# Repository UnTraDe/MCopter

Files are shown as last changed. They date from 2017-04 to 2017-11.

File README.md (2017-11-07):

# MCopter

A quadcopter built from scratch.

Currently there is a working PCB for the flight controller + basic firmware.

### Working (kind-of) features--

* Simple PID flight stabilization
* Radio communication via external radio module (both controlling the copter and sending telemtry data to the controller
* Simple remote controller made out of an old RC toy radio + arduino pro mini + nRF24

### Planned

* Designing custom frame and 3D print it
* Using an embedded radio solution (probably nRF24 based)
* Using 9-axis fusion instead of 6-axis to avoid yaw drift.

# The Hardware



This is version 2.0 of the flight controller PCB.
The PCB is design with 2 layers to keep down the cost, in the future I might redesign it with 4 layers to make it smaller. I'm also using 0805 to allow for easy hand-soldering.

The microcontroller is STM32F410RBT, a powerful 32-bit ARM Cortex M4 with hardware floating point unit and a lot of useful peripherals.

Other major components (sensors):

* ICM-20689; MEMES gyroscope + accelerometer. This is the newer generation of the popular MPU-6050 used in a lot of commercial flight controllers.
* MAG3110; A magnetometer.
* MS5637; A Barometer

The ICM-20689 togheter with the MAG3110 can be used for 9-axis fusion to provide better heading, avoid yaw drifting and togheter with the barometer also have an height based control instead of throttle based one.



* TODO take a better picture...

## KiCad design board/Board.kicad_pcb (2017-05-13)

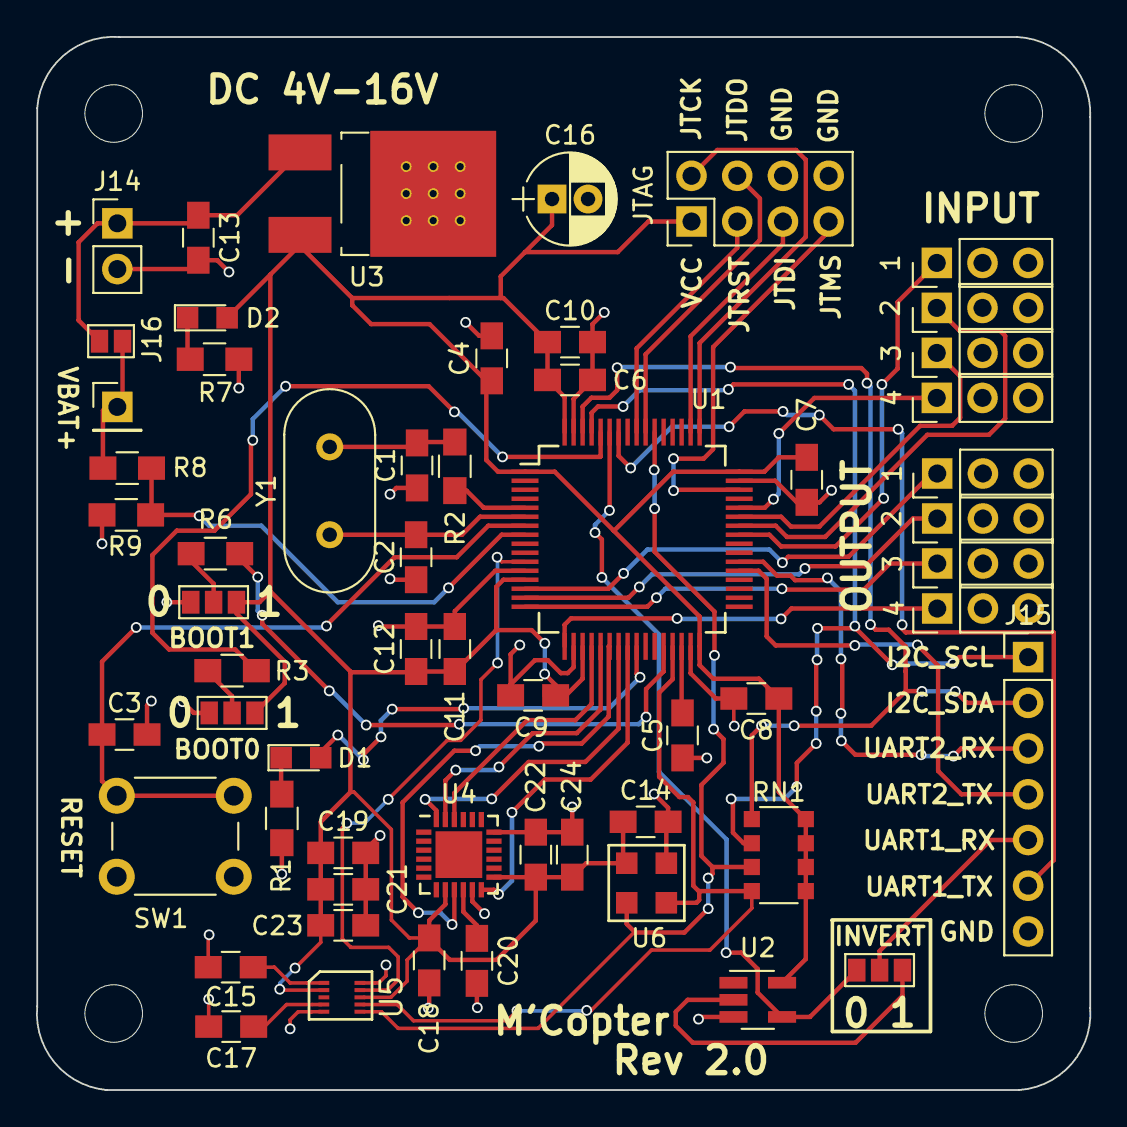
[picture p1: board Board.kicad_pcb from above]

Board: 2 copper layers, 58.5 x 58.5 mm, 54 parts (0 on the bottom side), 45 nets.

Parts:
1, 1#2, 2, 2#2, 3, 3#2, 4, 4#2: CONN_01X03; Pin_Header_Straight_1x03_Pitch2.54mm
C1, C2: 20pF; C_0805_HandSoldering
C3, C4, C6, C7, C8, C9, C12, C14, C15, C17, C21, C23, C24: 100nF; C_0805_HandSoldering
C5, C10: 4.7uF; C_0805_HandSoldering
C11, C19: 1uF; C_0805_HandSoldering
C13: 0.1uF; C_0805_HandSoldering
C16: 2.2uF; CP_Radial_D5.0mm_P2.00mm
C18: 10nF; C_0805_HandSoldering
C20: 0.47uF; C_0805_HandSoldering
C22: 2.2uF; C_0805_HandSoldering
D1, D2: LED; LED_0805
J14: CONN_01X02; Pin_Header_Straight_1x02_Pitch2.54mm
J15: CONN_01X07; Pin_Header_Straight_1x07_Pitch2.54mm
J16: GS2
JTAG: CONN_02X04; Pin_Header_Straight_2x04_Pitch2.54mm
R1: 22; R_0805_HandSoldering
R2: 0; R_0805_HandSoldering
R3, R6: 10K; R_0805_HandSoldering
R7: 220; R_0805_HandSoldering
R8: 62K; R_0805_HandSoldering
R9: 22K; R_0805_HandSoldering
RN1: 4.7K; R_Array_Convex_4x1206
SW1: SW_Push; SW_PUSH_6mm
U1: STM32F410RBTx; LQFP-64_10x10mm_Pitch0.5mm_handsoldering
U2: SN74LVC1G04; SOT-23-5_HandSoldering
U3: LF33ABDT-TR; TO-252-2Lead
U4: ICM-20689; QFN-24-1EP_4x4mm_Pitch0.5mm
U5: MAG3110; DFN_2x2mm_10pin_0.4pitch
U6: MS5637
Y1: 25 MHz; Crystal_HC49-U_Vertical

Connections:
+BATT: C13.1, J14.1, J16.1, U3.1
BATT_ADC: R8.2, R9.1, U1.8
GND: 1.3, 1#2.3, 2.3, 2#2.3, 3.3, 3#2.3, 4.3, 4#2.3, C1.1, C2.1, C3.2, C4.2, C5.2, C6.2, C7.2, C8.2, C9.2, C10.2, C11.2, C12.2, C13.2, C14.2, C15.2, C16.2, C17.2, C18.2, C19.2, C20.2, C21.2, C22.2, C23.2, C24.2, J14.2, J15.7, JTAG.6, JTAG.8, R1.2, R7.2, R9.2, SW1.1, U1.12, U1.18, U1.31, U1.47, U1.63, U2.3, U3.2, U4.11, U4.18, U5.5, U5.10, U6.4
I2C1_SCL: J15.1, RN1.2, U1.61
I2C1_SDA: J15.2, RN1.1, U1.62
I2C2_SCL: RN1.4, U1.29, U5.7, U6.3
I2C2_SDA: RN1.3, U1.54, U5.6, U6.2
ICM_INT: U1.24, U4.12
ICM_SPI_CS: U1.20, U4.22
ICM_SPI_MISO: U1.22, U4.9
ICM_SPI_MOSI: U1.23, U4.24
ICM_SPI_SCK: U1.21, U4.23
JTCK: JTAG.2, U1.49
JTDI: JTAG.5, U1.50
JTDO: JTAG.4, U1.55
JTMS: JTAG.7, U1.46
JTRST: JTAG.3, U1.56
MAG_INT: U1.11, U5.9
unnamed: C1.2, R2.1, Y1.2
unnamed: C2.2, U1.6, Y1.1
unnamed: C3.1, SW1.2, U1.7
unnamed: C5.1, U1.30
unnamed: C15.1, U5.1
unnamed: C17.1, U5.4
unnamed: C20.1, U4.10
unnamed: D1.1, R1.1
unnamed: D1.2, U1.25
unnamed: D2.1, R7.1
unnamed: J16.2, R8.1
unnamed: R2.2, U1.5
unnamed: R3.2, U1.60
unnamed: R6.1, U1.28
PWM_INPUT_1: 1#2.1, U1.41
PWM_INPUT_2: 2#2.1, U1.42
PWM_INPUT_3: 3#2.1, U1.43
PWM_INPUT_4: 4#2.1, U1.44
PWM_OUTPUT_1: 1.1, U1.14
PWM_OUTPUT_2: 2.1, U1.15
PWM_OUTPUT_3: 3.1, U1.16
PWM_OUTPUT_4: 4.1, U1.17
UART1_RX: U1.59, U2.4
UART1_TX: J15.6, U1.58
UART2_RX: J15.3, U1.38
UART2_TX: J15.4, U1.37
VCC: C4.1, C6.1, C7.1, C8.1, C9.1, C10.1, C11.1, C12.1, C14.1, C16.1, C18.1, C19.1, C21.1, C22.1, C23.1, C24.1, D2.2, JTAG.1, RN1.5, RN1.6, RN1.7, RN1.8, U1.1, U1.13, U1.19, U1.32, U1.48, U1.64, U2.5, U3.3, U4.8, U4.13, U5.2, U5.8, U6.1

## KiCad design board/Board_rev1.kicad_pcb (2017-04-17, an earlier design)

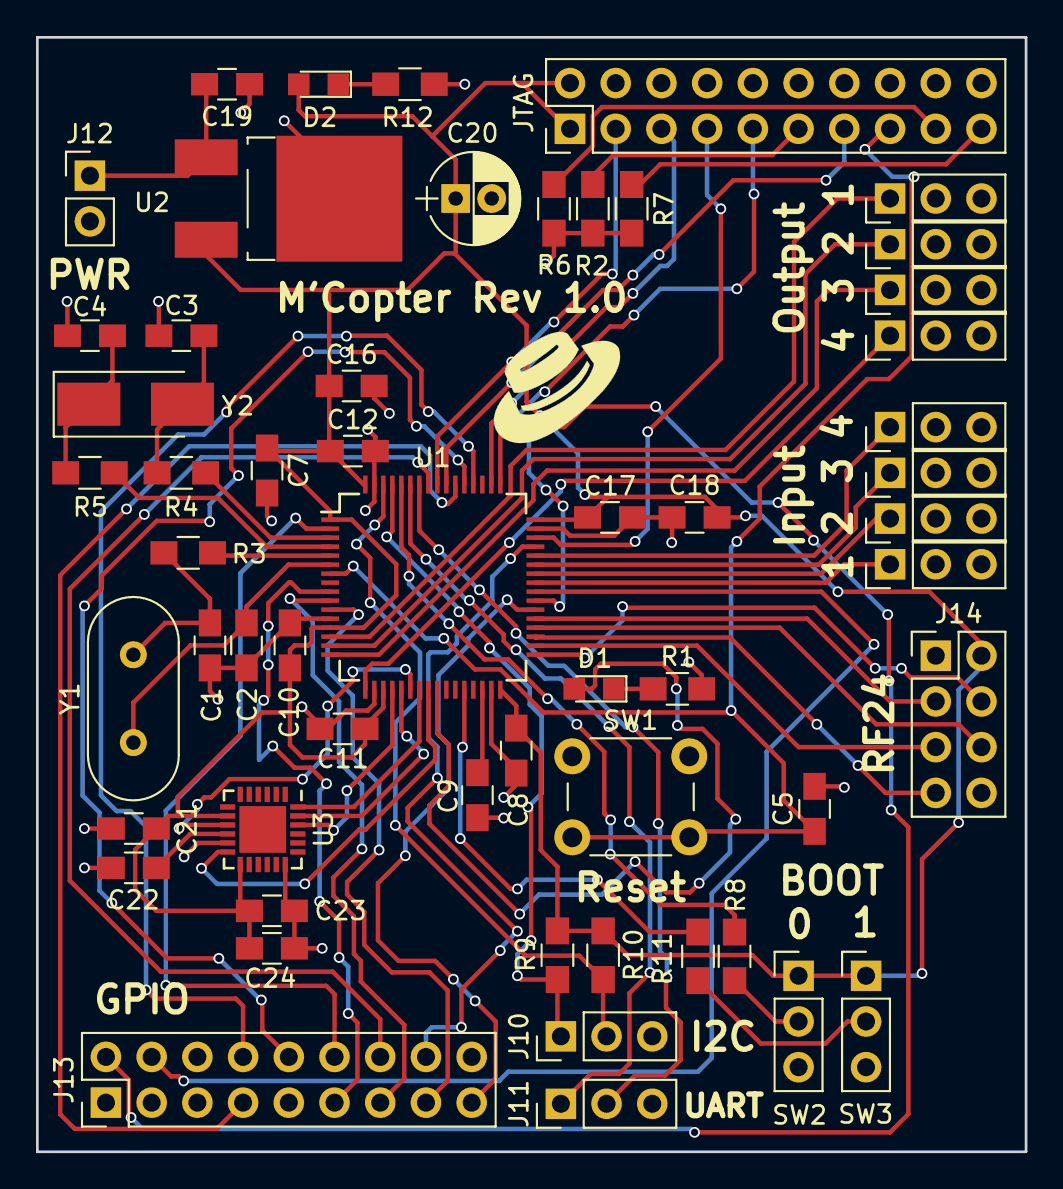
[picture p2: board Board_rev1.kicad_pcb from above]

Board: 2 copper layers, 54.9 x 61.9 mm, 48 parts (0 on the bottom side), 54 nets.

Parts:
C1, C2: 20pF; C_0805_HandSoldering
C3, C4: 1.5pF; C_0805_HandSoldering
C5, C7, C8, C10, C11, C12, C18, C24: 100nF; C_0805_HandSoldering
C9, C16: 4.7uF; C_0805_HandSoldering
C17: 1uF; C_0805_HandSoldering
C19: 0.1uF; C_0805_HandSoldering
C20: 2.2uF; CP_Radial_D5.0mm_P2.00mm
C21: 10nF; C_0805_HandSoldering
C22: 0.47uF; C_0805_HandSoldering
C23: 2.2uF; C_0805_HandSoldering
D1, D2: LED; LED_0805
J10, J11: CONN_01X03; Pin_Header_Straight_1x03_Pitch2.54mm
J12: CONN_01X02; Pin_Header_Straight_1x02_Pitch2.54mm
J13: CONN_02X09; Pin_Header_Straight_2x09_Pitch2.54mm
J14: CONN_02X04; Pin_Header_Straight_2x04_Pitch2.54mm
JTAG: CONN_02X10; Pin_Header_Straight_2x10_Pitch2.54mm
R1: 22; R_0805_HandSoldering
R2, R6, R7, R8, R9, R10, R11: 10K; R_0805_HandSoldering
R3, R4, R5: 0; R_0805_HandSoldering
R12: 220; R_0805_HandSoldering
SW1: SW_Push; SW_PUSH_6mm
SW2, SW3: SW_SPDT; Pin_Header_Straight_1x03_Pitch2.54mm
U1: STM32F410RBTx; LQFP-64_10x10mm_Pitch0.5mm
U2: LF33ABDT-TR; TO-252-2Lead
U3: ICM-20689; QFN-24-1EP_4x4mm_Pitch0.5mm
Y1: 25 MHz; Crystal_HC49-U_Vertical
Y2: 32.768 KHz; Crystal_SMD_5032-2pin_5.0x3.2mm_HandSoldering

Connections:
+12V: C19.1, J12.1, U2.1
GND: C1.1, C2.1, C3.1, C4.1, C5.2, C7.2, C8.2, C9.2, C10.2, C11.2, C12.2, C16.2, C17.2, C18.2, C19.2, C20.2, C21.2, C22.2, C23.2, C24.2, J10.3, J11.3, J12.2, J13.18, J14.1, JTAG.4, JTAG.6, JTAG.8, JTAG.10, JTAG.12, JTAG.14, JTAG.16, JTAG.18, JTAG.20, R1.2, R2.2, R6.2, R7.2, R12.2, SW1.1, SW2.3, SW3.3, U1.12, U1.18, U1.31, U1.47, U1.63, U2.2, U3.11, U3.18
I2C_SCL: J10.1, R9.2, U1.61
I2C_SDA: J10.2, R10.2, U1.62
ICM_INT: U1.24, U3.12
ICM_SPI_CS: U1.20, U3.22
ICM_SPI_MISO: U1.22, U3.9
ICM_SPI_MOSI: U1.23, U3.24
ICM_SPI_SCK: U1.21, U3.23
JTCK: JTAG.9, U1.49
JTDI: JTAG.5, U1.50
JTDO: JTAG.13, U1.55
JTMS: JTAG.7, U1.46
JTRST: JTAG.3, U1.56
NRF24_CE: J14.3, U1.37
NRF24_SPI_CS: J14.4, U1.33
NRF24_SPI_MISO: J14.7, U1.35
NRF24_SPI_MOSI: J14.6, U1.36
NRF24_SPI_SCK: J14.5, U1.34
NRST: C5.1, JTAG.15, SW1.2, U1.7
unnamed: C1.2, R3.1, Y1.2
unnamed: C2.2, U1.6, Y1.1
unnamed: C3.2, R4.1, Y2.2
unnamed: C4.2, R5.1, Y2.1
unnamed: C9.1, U1.30
unnamed: C22.1, U3.10
unnamed: D1.1, R1.1
unnamed: D1.2, U1.25
unnamed: D2.1, R12.1
unnamed: JTAG.11, R2.1
unnamed: JTAG.17, R6.1
unnamed: JTAG.19, R7.1
unnamed: R3.2, U1.5
unnamed: R4.2, U1.3
unnamed: R5.2, U1.4
unnamed: R8.1, SW2.2
unnamed: R8.2, U1.60
unnamed: R11.1, U1.28
unnamed: R11.2, SW3.2
PA12: J13.16, U1.45
PB5: J13.14, U1.57
PB11: J13.7, U1.54
PC1: J13.11, U1.9
PC2: J13.13, U1.10
PC3: J13.15, U1.11
PC7: J13.17, U1.38
PC8: J13.2, U1.39
PC9: J13.4, U1.40
PC11: J13.8, U1.52
PC12: J13.10, U1.53
PC13: J13.12, U1.2
UART_RX: J11.1, U1.59
UART_TX: J11.2, U1.58
VCC: C7.1, C8.1, C10.1, C11.1, C12.1, C16.1, C17.1, C18.1, C20.1, C21.1, C23.1, C24.1, D2.2, J14.2, JTAG.1, JTAG.2, R9.1, R10.1, SW2.1, SW3.1, U1.1, U1.13, U1.19, U1.32, U1.48, U1.64, U2.3, U3.8, U3.13

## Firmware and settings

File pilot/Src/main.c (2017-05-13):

/**
  ******************************************************************************
  * File Name          : main.c
  * Description        : Main program body
  ******************************************************************************
  *
  * COPYRIGHT(c) 2017 STMicroelectronics
  *
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
  ******************************************************************************
  */
/* Includes ------------------------------------------------------------------*/
#include "main.h"
#include "stm32f4xx_hal.h"

/* USER CODE BEGIN Includes */

#include <string.h>

#include "ICM20689.h"
#include "MS5637.h"
#include "AxisFusion.h"
#include "Common.h"
#include "Quaternion.h"
#include "Motors.h"
#include "PID.h"

/* USER CODE END Includes */

ADC_HandleTypeDef hadc1;

I2C_HandleTypeDef hi2c1;
I2C_HandleTypeDef hi2c2;

SPI_HandleTypeDef hspi1;
SPI_HandleTypeDef hspi2;

TIM_HandleTypeDef htim1;
TIM_HandleTypeDef htim5;

UART_HandleTypeDef huart1;
UART_HandleTypeDef huart6;
DMA_HandleTypeDef hdma_usart1_rx;

void SystemClock_Config(void);
void Error_Handler(void);
static void MX_GPIO_Init(void);
static void MX_DMA_Init(void);
static void MX_I2C1_Init(void);
static void MX_SPI1_Init(void);
static void MX_SPI2_Init(void);
static void MX_TIM1_Init(void);
static void MX_TIM5_Init(void);
static void MX_USART1_UART_Init(void);
static void MX_USART6_UART_Init(void);
static void MX_I2C2_Init(void);
static void MX_ADC1_Init(void);

void HAL_TIM_MspPostInit(TIM_HandleTypeDef *htim);
                                

/* USER CODE BEGIN 0 */

static const float Kp = 3.0f;
static const float Ki = 0.08f;
static const float Kd = 10.0f;
static const float i_limit = 100.0f;

static const float Kp_yaw = 8.0f;
static const float Ki_yaw = 0.4f;
static const float Kd_yaw = 0.0f;
static const float i_limit_yaw = 40.0f;

static const float _control_angle = 30.0f;
static const float _yaw_max_rate = 60.0f;

static volatile uint8_t _imu_data_ready = 0;
static volatile uint16_t _missed_imu_data = 0;

static float _orientation[4] = { 1.0f, 0.0f, 0.0f, 0.0f }; // Quaternion
static float _reference_orientation[4] = { 1.0f, 0.0f, 0.0f, 0.0f };

static uint16_t _throttle = 0;
static float _target_yaw_rate = 0.0f;
static float _target_pitch = 0.0f;
static float _target_roll = 0.0f;

static PID _pid_pitch;
static PID _pid_roll;
static PID _pid_yaw;

static volatile uint8_t _receiver_data_ready = 0;
static volatile struct
{
	uint16_t channels[16];
	uint8_t fail_safe;
} _receiver_data;

#define BATTERY_VOLTAGE_PERIOD		1000
#define BATTERY_LOW_THRESHOLD		10.8f
#define BATTERY_VOLTAGE_MULTIPLIER	3.794f
#define THROTTLE_THRESHOLD			150

#define SBUS_CHANNEL_MIN 				172
#define SBUS_CHANNEL_MAX 				1811
#define SBUS_CHANENL_RANGE				(SBUS_CHANNEL_MAX - SBUS_CHANNEL_MIN)

void HAL_GPIO_EXTI_Callback(uint16_t GPIO_Pin)
{
	if (GPIO_Pin == GPIO_PIN_4)
	{
		// TODO need to disable interrupts before doing SPI stuff?
		
		if (!_imu_data_ready)
		{
			if (ICM20689_DataReady())
				_imu_data_ready = 1;
		}
		else
		{
			_missed_imu_data++;
		}
		
		// TODO handle cases where the interrupt was generated because of another reason... 
	}	
}

static uint8_t _uart_rx_data_buffer[32];
static uint8_t _uart_tx_data_buffer[32];

void HAL_UART_RxCpltCallback(UART_HandleTypeDef* huart)
{
	if (!_receiver_data_ready)
	{
		if (_uart_rx_data_buffer[0] == 0x0F && _uart_rx_data_buffer[24] == 0x00)
		{
			uint8_t* payload = &_uart_rx_data_buffer[1];
		
			_receiver_data.channels[0]  = (uint16_t)((payload[0]    | payload[1] << 8) & 0x07FF);
			_receiver_data.channels[1]  = (uint16_t)((payload[1] >> 3 | payload[2] << 5) & 0x07FF);
			_receiver_data.channels[2]  = (uint16_t)((payload[2] >> 6 | payload[3] << 2 | payload[4] << 10) & 0x07FF);
			_receiver_data.channels[3]  = (uint16_t)((payload[4] >> 1 | payload[5] << 7) & 0x07FF);
			_receiver_data.channels[4]  = (uint16_t)((payload[5] >> 4 | payload[6] << 4) & 0x07FF);
			_receiver_data.channels[5]  = (uint16_t)((payload[6] >> 7 | payload[7] << 1 | payload[8] << 9) & 0x07FF);
			_receiver_data.channels[6]  = (uint16_t)((payload[8] >> 2 | payload[9] << 6) & 0x07FF);
			_receiver_data.channels[7]  = (uint16_t)((payload[9] >> 5 | payload[10] << 3) & 0x07FF);
			_receiver_data.channels[8]  = (uint16_t)((payload[11]   | payload[12] << 8) & 0x07FF);
			_receiver_data.channels[9]  = (uint16_t)((payload[12] >> 3 | payload[13] << 5) & 0x07FF);
			_receiver_data.channels[10] = (uint16_t)((payload[13] >> 6 | payload[14] << 2 | payload[15] << 10) & 0x07FF);
			_receiver_data.channels[11] = (uint16_t)((payload[15] >> 1 | payload[16] << 7) & 0x07FF);
			_receiver_data.channels[12] = (uint16_t)((payload[16] >> 4 | payload[17] << 4) & 0x07FF);
			_receiver_data.channels[13] = (uint16_t)((payload[17] >> 7 | payload[18] << 1 | payload[19] << 9) & 0x07FF);
			_receiver_data.channels[14] = (uint16_t)((payload[19] >> 2 | payload[20] << 6) & 0x07FF);
			_receiver_data.channels[15] = (uint16_t)((payload[20] >> 5 | payload[21] << 3) & 0x07FF);
			
			_receiver_data.fail_safe = (payload[22] & 0x08);
		
			_receiver_data_ready = 1;
		}
	}
	else
	{
		// TODO increment some dropped counter
	}
	
	// TODO can this be replaced by configuring the DMA as circular?
	HAL_UART_Receive_DMA(&huart1, _uart_rx_data_buffer, 25);
}

static void CalculateBias(float* gyro_bias, float* accel_bias);

/* USER CODE END 0 */

int main(void)
{

  /* MCU Configuration----------------------------------------------------------*/

  /* Reset of all peripherals, Initializes the Flash interface and the Systick. */
	HAL_Init();

	  /* Configure the system clock */
	SystemClock_Config();

	  /* Initialize all configured peripherals */
	MX_GPIO_Init();
	MX_DMA_Init();
	MX_I2C1_Init();
	MX_SPI1_Init();
	MX_SPI2_Init();
	MX_TIM1_Init();
	MX_TIM5_Init();
	MX_USART1_UART_Init();
	MX_USART6_UART_Init();
	MX_I2C2_Init();
	MX_ADC1_Init();

	  /* USER CODE BEGIN 2 */
	Motors_Init(&htim5);
	
	uint8_t error = ICM20689_Init(&hspi1, GPIOA, GPIO_PIN_4);
	
	if (error)
	{
		while (1)
		{
			HAL_GPIO_TogglePin(GPIOC, GPIO_PIN_5);
			HAL_Delay(500);
		}
	}
	
	_pid_pitch.kp = Kp;
	_pid_pitch.ki = Ki;
	_pid_pitch.kd = Kd;
	_pid_pitch.i_limit = i_limit;
	_pid_pitch.error_sum = 0.0f;
	_pid_pitch.last_error = 0.0f;
	_pid_pitch.error = 0.0f;
	_pid_pitch.error_rate = 0.0f;
	
	_pid_roll.kp = Kp;
	_pid_roll.ki = Ki;
	_pid_roll.kd = Kd;
	_pid_roll.i_limit = i_limit;
	_pid_roll.error_sum = 0.0f;
	_pid_roll.last_error = 0.0f;
	_pid_roll.error = 0.0f;
	_pid_roll.error_rate = 0.0f;
	
	_pid_yaw.kp = Kp_yaw;
	_pid_yaw.ki = Ki_yaw;
	_pid_yaw.kd = Kd_yaw;
	_pid_yaw.i_limit = i_limit_yaw;
	_pid_yaw.error_sum = 0.0f;
	_pid_yaw.last_error = 0.0f;
	_pid_yaw.error = 0.0f;
	_pid_yaw.error_rate = 0.0f;
	
  /* USER CODE END 2 */

  /* Infinite loop */
  /* USER CODE BEGIN 3 */
	
	

	float gyro_bias[3] = { 0.503540, 1.441956, 0.129700 };
	float accel_bias[3] = { -0.000305, -0.004944, 0.017456 };
//	CalculateBias(gyro_bias, accel_bias);
//	
//	uint8_t output[128] = { 0 };
//	sprintf((char*)output, "%f, %f, %f\r\n%f, %f, %f\r\n", gyro_bias[0], gyro_bias[1], gyro_bias[2], accel_bias[0], accel_bias[1], accel_bias[2]);
//	HAL_UART_Transmit(&huart6, output, strlen((char*)output), 100);
	
	gyro_bias[0] *= -1;
	gyro_bias[1] *= -1;
	gyro_bias[2] *= -1;
	ICM20689_SetLocalGyroBias(gyro_bias);
	
	accel_bias[0] *= -1;
	accel_bias[1] *= -1;
	accel_bias[2] *= -1;
	ICM20689_SetLocalAccelBias(accel_bias);
	
	// SBUS is sending every 4 ms, so we wait to synchronize
	
	while (1)
	{
		if (HAL_TIMEOUT == HAL_UART_Receive(&huart1, _uart_rx_data_buffer, 1, 2))
		{
			HAL_UART_Receive_DMA(&huart1, _uart_rx_data_buffer, 25);
			break;
		}
	}
	
	uint8_t fail_safe = 1;
	
	uint32_t now = HAL_GetTick();
	uint32_t last = now;
	
	uint32_t battery_voltage_timer = 0;
	uint32_t test_timer = 0;
	uint32_t hz_timer = 0;
	
	uint32_t hz_counter = 0;
	
	uint8_t cmd;
	
	// Barometer test
	
	//MS5637_Init(&hi2c2, 0x76);
	
//	cmd = 0x1E;
//	if (HAL_I2C_Master_Transmit(&hi2c2, 0b11101100, &cmd, 1, 100) != HAL_OK)
//	{
//		while (1)
//		{
//			HAL_GPIO_TogglePin(GPIOC, GPIO_PIN_5);
//			HAL_Delay(500);
//		}
//	}
//	
//	cmd = 0xA0;
//	HAL_I2C_Master_Transmit(&hi2c2, 0b11101100, &cmd, 1, 100);
//	uint16_t data = 0;
//	HAL_I2C_Master_Receive(&hi2c2, 0b11101101, (uint8_t*)&data, 2, 100);
	
	// Magnetometer test
	
//	cmd = 0x07;
//	HAL_I2C_Master_Transmit(&hi2c2, 0x0E << 1, &cmd, 1, 100);
//	uint8_t id = 0;
//	HAL_I2C_Master_Receive(&hi2c2, (0x0E << 1) | 0x01, (uint8_t*)&id, 1, 100);
	
	float battery_voltage = 12.6f;
	float battery_voltage_idle = 12.6f;
	
	// TODO intialize those with actual values from the ADC
	
	while (1)
	{
		now = HAL_GetTick(); // TODO handle rollover
		uint32_t dt_ms = now - last;
		last = now;
		
		battery_voltage_timer += dt_ms;
		test_timer += dt_ms;
		hz_timer += dt_ms;
		
		if (_receiver_data_ready)
		{
			uint16_t throttle = ((_receiver_data.channels[0] - SBUS_CHANNEL_MIN) / (float)SBUS_CHANENL_RANGE) * 1000.0f;
			
			if (throttle > 800)
				_throttle = 800;
			else
				_throttle = throttle;
			
//			
//			if (throttle > 500)
//				throttle = 1000;
//			else
//				throttle = 0;
//			
//			float motors[4];
//			
//			motors[0] = throttle; // Back Right
//			motors[1] = throttle; // Back Left
//			motors[2] = throttle; // Front Right
//			motors[3] = throttle; // Front Left
//
//			Motors_Set(motors);
			
			_target_yaw_rate = ((_receiver_data.channels[3] - SBUS_CHANNEL_MIN) * (_yaw_max_rate / SBUS_CHANENL_RANGE)) - (_yaw_max_rate / 2.0f);
			_target_pitch = ((_receiver_data.channels[2] - SBUS_CHANNEL_MIN) * (_control_angle / SBUS_CHANENL_RANGE)) - (_control_angle / 2.0f);
			_target_roll = ((_receiver_data.channels[1] - SBUS_CHANNEL_MIN) * (_control_angle / SBUS_CHANENL_RANGE)) - (_control_angle / 2.0f);

			_target_yaw_rate *= -1;
			
			fail_safe = _receiver_data.fail_safe;
			
//			if (test_timer >= 10)
//			{
//				test_timer = 0;
//				uint8_t output[32] = { 0 };
//				sprintf((char*)output, "%f, %f, %f\r\n", _target_pitch, _target_yaw_rate, _target_roll);
//				HAL_UART_Transmit(&huart6, output, strlen((char*)output), 100);
//			}
			
			_receiver_data_ready = 0;
		}
		
//		if (test_timer >= 10)
//		{
//			test_timer = 0;
//			uint8_t output[64] = { 0 };
//			sprintf((char*)output, "%d, %d\r\n", fail_safe, _throttle);
//			HAL_UART_Transmit(&huart6, output, strlen((char*)output), 1000);
//		}
		
		if (fail_safe)
		{
			float motors[4] = { 0 };
			Motors_Set(motors);
			continue;
		}
		
//		if (battery_voltage_timer >= BATTERY_VOLTAGE_PERIOD)
//		{
//			battery_voltage_timer = 0;
//			
//			HAL_StatusTypeDef status = HAL_ADC_Start(&hadc1);
//			status = HAL_ADC_PollForConversion(&hadc1, 10);
//		
//			if (status != HAL_TIMEOUT)
//			{
//				uint32_t val = HAL_ADC_GetValue(&hadc1);
//				float voltage = (3.3f / 4096.0f) * val;
//				battery_voltage = voltage * BATTERY_VOLTAGE_MULTIPLIER;
//				
//				if (_throttle < THROTTLE_THRESHOLD)
//					battery_voltage_idle = voltage * BATTERY_VOLTAGE_MULTIPLIER;
//				
////				uint8_t output[64] = { 0 };
////				sprintf((char*)output, "%d, %f, %f\r\n", _throttle, battery_voltage, battery_voltage_idle);
////				HAL_UART_Transmit(&huart6, output, strlen((char*)output), 1000);
//				
//				// TODO averaging samples?
//			}
//			else
//			{
//				battery_voltage = 0.0f;
//			}
//		
//			HAL_ADC_Stop(&hadc1);
//		}
		
//		if (battery_voltage_idle <= BATTERY_LOW_THRESHOLD)
//		{
//			float motors[4] = { 0 };
//			Motors_Set(motors);
//			
//			HAL_GPIO_WritePin(GPIOC, GPIO_PIN_5, GPIO_PIN_SET);
//			HAL_Delay(200);
//			HAL_GPIO_WritePin(GPIOC, GPIO_PIN_5, GPIO_PIN_RESET);
//			HAL_Delay(200);
//			HAL_GPIO_WritePin(GPIOC, GPIO_PIN_5, GPIO_PIN_SET);
//			HAL_Delay(200);
//			HAL_GPIO_WritePin(GPIOC, GPIO_PIN_5, GPIO_PIN_RESET);
//			HAL_Delay(1000);
//		}
		
		if (_imu_data_ready)
		{
			_imu_data_ready = 0;
			
			float gyro[3];
			float accel[3];
			ICM20689_ReadGyro(gyro);
			ICM20689_ReadAccel(accel);
//			
//			hz_counter++;
//			
//			if (hz_timer >= 1000)
//			{
//				hz_timer = 0;
//				uint8_t output[16] = { 0 };
//				sprintf((char*)output, "%d\r\n", hz_counter);
//				hz_counter = 0;
//				HAL_UART_Transmit(&huart6, output, strlen((char*)output), 100);
//			}
			
			AxisFusion_MahonyAHRSupdateIMU(_orientation, gyro[0]*PI / 180.0f, gyro[1]*PI / 180.0f, gyro[2]*PI / 180.0f, accel[0], accel[1], accel[2]);
		
			float quat[4];
			Quaternion_Multiply(_reference_orientation, _orientation, quat);
		
			float pitch, roll, yaw;
			Quaternion_ToEuler(quat, &pitch, &roll, &yaw);
		
			pitch *= 180.0f / PI;
			yaw *= 180.0f / PI;
			roll *= 180.0f / PI;
			
//			if (test_timer >= 100)
//			{
//				test_timer = 0;
//				uint8_t output[32] = { 0 };
//				sprintf((char*)output, "%.2f, %.2f, %.2f\r\n", pitch, yaw, roll);
//				HAL_UART_Transmit(&huart6, output, strlen((char*)output), 100);
//			}
			
			float output_pitch = 0.0f;
			float output_roll = 0.0f;
			float output_yaw = 0.0f;
			
			float dt_ms = 0.01f; // TODO IMPORTANTTTTTTTTTTTTTTTTTTTTTTTTTTTTTTTTTTTTTTTTTTTTTTTTTTTTTTTTTTTTTTTTTTTTT

			if (_throttle >= THROTTLE_THRESHOLD)
			{
				output_pitch = PID_Compute(&_pid_pitch, _target_pitch, pitch, dt_ms);
				output_roll = PID_Compute(&_pid_roll, _target_roll, roll, dt_ms);
				output_yaw = PID_Compute(&_pid_yaw, _target_yaw_rate, gyro[2] * (PI / 180.0f), dt_ms);
			}
			else
			{
				_pid_pitch.error_sum = 0.0f;
				_pid_roll.error_sum = 0.0f;
				_pid_yaw.error_sum = 0.0f;
			}
	
			float motors[4];
			
			motors[0] = _throttle + output_pitch - output_roll + output_yaw; // Back Right
			motors[1] = _throttle + output_pitch + output_roll - output_yaw; // Back Left
			motors[2] = _throttle - output_pitch - output_roll - output_yaw; // Front Right
			motors[3] = _throttle - output_pitch + output_roll + output_yaw; // Front Left
			
			Motors_Set(motors);
			
//			if (test_timer >= 10)
//			{
//				test_timer = 0;
//				uint8_t output[64] = { 0 };
//				sprintf((char*)output, "%.2f, %.2f, %.2f\r\n", output_pitch, output_roll, output_yaw);
//				HAL_UART_Transmit(&huart6, output, strlen((char*)output), 1000);
//			}
			
//			if (test_timer >= 10)
//			{
//				test_timer = 0;
//				uint8_t output[64] = { 0 };
//				sprintf((char*)output, "%.2f, %.2f, %.2f, %.2f\n", motors[0], motors[1], motors[2], motors[3]);
//				HAL_UART_Transmit(&huart6, output, strlen((char*)output), 1000);
//			}

			
		}
	}
	
  /* USER CODE END 3 */

}

/** System Clock Configuration
*/
void SystemClock_Config(void)
{

	RCC_OscInitTypeDef RCC_OscInitStruct;
	RCC_ClkInitTypeDef RCC_ClkInitStruct;

	    /**Configure the main internal regulator output voltage 
	    */
	__HAL_RCC_PWR_CLK_ENABLE();

	__HAL_PWR_VOLTAGESCALING_CONFIG(PWR_REGULATOR_VOLTAGE_SCALE1);

	    /**Initializes the CPU, AHB and APB busses clocks 
	    */
	RCC_OscInitStruct.OscillatorType = RCC_OSCILLATORTYPE_HSE;
	RCC_OscInitStruct.HSEState = RCC_HSE_ON;
	RCC_OscInitStruct.PLL.PLLState = RCC_PLL_ON;
	RCC_OscInitStruct.PLL.PLLSource = RCC_PLLSOURCE_HSE;
	RCC_OscInitStruct.PLL.PLLM = 12;
	RCC_OscInitStruct.PLL.PLLN = 96;
	RCC_OscInitStruct.PLL.PLLP = RCC_PLLP_DIV2;
	RCC_OscInitStruct.PLL.PLLQ = 4;
	RCC_OscInitStruct.PLL.PLLR = 2;
	if (HAL_RCC_OscConfig(&RCC_OscInitStruct) != HAL_OK)
	{
		Error_Handler();
	}

	    /**Initializes the CPU, AHB and APB busses clocks 
	    */
	RCC_ClkInitStruct.ClockType = RCC_CLOCKTYPE_HCLK | RCC_CLOCKTYPE_SYSCLK
	                            | RCC_CLOCKTYPE_PCLK1 | RCC_CLOCKTYPE_PCLK2;
	RCC_ClkInitStruct.SYSCLKSource = RCC_SYSCLKSOURCE_PLLCLK;
	RCC_ClkInitStruct.AHBCLKDivider = RCC_SYSCLK_DIV1;
	RCC_ClkInitStruct.APB1CLKDivider = RCC_HCLK_DIV4;
	RCC_ClkInitStruct.APB2CLKDivider = RCC_HCLK_DIV1;

	if (HAL_RCC_ClockConfig(&RCC_ClkInitStruct, FLASH_LATENCY_3) != HAL_OK)
	{
		Error_Handler();
	}

	    /**Configure the Systick interrupt time 
	    */
	HAL_SYSTICK_Config(HAL_RCC_GetHCLKFreq() / 1000);

	    /**Configure the Systick 
	    */
	HAL_SYSTICK_CLKSourceConfig(SYSTICK_CLKSOURCE_HCLK);

	  /* SysTick_IRQn interrupt configuration */
	HAL_NVIC_SetPriority(SysTick_IRQn, 0, 0);
}

/* ADC1 init function */
static void MX_ADC1_Init(void)
{

	ADC_ChannelConfTypeDef sConfig;

	    /**Configure the global features of the ADC (Clock, Resolution, Data Alignment and number of conversion) 
	    */
	hadc1.Instance = ADC1;
	hadc1.Init.ClockPrescaler = ADC_CLOCK_SYNC_PCLK_DIV4;
	hadc1.Init.Resolution = ADC_RESOLUTION_12B;
	hadc1.Init.ScanConvMode = DISABLE;
	hadc1.Init.ContinuousConvMode = DISABLE;
	hadc1.Init.DiscontinuousConvMode = DISABLE;
	hadc1.Init.ExternalTrigConvEdge = ADC_EXTERNALTRIGCONVEDGE_NONE;
	hadc1.Init.ExternalTrigConv = ADC_SOFTWARE_START;
	hadc1.Init.DataAlign = ADC_DATAALIGN_RIGHT;
	hadc1.Init.NbrOfConversion = 1;
	hadc1.Init.DMAContinuousRequests = DISABLE;
	hadc1.Init.EOCSelection = ADC_EOC_SINGLE_CONV;
	if (HAL_ADC_Init(&hadc1) != HAL_OK)
	{
		Error_Handler();
	}

	    /**Configure for the selected ADC regular channel its corresponding rank in the sequencer and its sample time. 
	    */
	sConfig.Channel = ADC_CHANNEL_10;
	sConfig.Rank = 1;
	sConfig.SamplingTime = ADC_SAMPLETIME_3CYCLES;
	if (HAL_ADC_ConfigChannel(&hadc1, &sConfig) != HAL_OK)
	{
		Error_Handler();
	}

}

/* I2C1 init function */
static void MX_I2C1_Init(void)
{

	hi2c1.Instance = I2C1;
	hi2c1.Init.ClockSpeed = 100000;
	hi2c1.Init.DutyCycle = I2C_DUTYCYCLE_2;
	hi2c1.Init.OwnAddress1 = 0;
	hi2c1.Init.AddressingMode = I2C_ADDRESSINGMODE_7BIT;
	hi2c1.Init.DualAddressMode = I2C_DUALADDRESS_DISABLE;
	hi2c1.Init.OwnAddress2 = 0;
	hi2c1.Init.GeneralCallMode = I2C_GENERALCALL_DISABLE;
	hi2c1.Init.NoStretchMode = I2C_NOSTRETCH_DISABLE;
	if (HAL_I2C_Init(&hi2c1) != HAL_OK)
	{
		Error_Handler();
	}

}

/* I2C2 init function */
static void MX_I2C2_Init(void)
{

	hi2c2.Instance = I2C2;
	hi2c2.Init.ClockSpeed = 400000;
	hi2c2.Init.DutyCycle = I2C_DUTYCYCLE_2;
	hi2c2.Init.OwnAddress1 = 0;
	hi2c2.Init.AddressingMode = I2C_ADDRESSINGMODE_7BIT;
	hi2c2.Init.DualAddressMode = I2C_DUALADDRESS_DISABLE;
	hi2c2.Init.OwnAddress2 = 0;
	hi2c2.Init.GeneralCallMode = I2C_GENERALCALL_DISABLE;
	hi2c2.Init.NoStretchMode = I2C_NOSTRETCH_DISABLE;
	if (HAL_I2C_Init(&hi2c2) != HAL_OK)
	{
		Error_Handler();
	}

}

/* SPI1 init function */
static void MX_SPI1_Init(void)
{

	hspi1.Instance = SPI1;
	hspi1.Init.Mode = SPI_MODE_MASTER;
	hspi1.Init.Direction = SPI_DIRECTION_2LINES;
	hspi1.Init.DataSize = SPI_DATASIZE_8BIT;
	hspi1.Init.CLKPolarity = SPI_POLARITY_HIGH;
	hspi1.Init.CLKPhase = SPI_PHASE_2EDGE;
	hspi1.Init.NSS = SPI_NSS_SOFT;
	hspi1.Init.BaudRatePrescaler = SPI_BAUDRATEPRESCALER_16;
	hspi1.Init.FirstBit = SPI_FIRSTBIT_MSB;
	hspi1.Init.TIMode = SPI_TIMODE_DISABLE;
	hspi1.Init.CRCCalculation = SPI_CRCCALCULATION_DISABLE;
	hspi1.Init.CRCPolynomial = 15;
	if (HAL_SPI_Init(&hspi1) != HAL_OK)
	{
		Error_Handler();
	}

}

/* SPI2 init function */
static void MX_SPI2_Init(void)
{

	hspi2.Instance = SPI2;
	hspi2.Init.Mode = SPI_MODE_MASTER;
	hspi2.Init.Direction = SPI_DIRECTION_2LINES;
	hspi2.Init.DataSize = SPI_DATASIZE_8BIT;
	hspi2.Init.CLKPolarity = SPI_POLARITY_LOW;
	hspi2.Init.CLKPhase = SPI_PHASE_1EDGE;
	hspi2.Init.NSS = SPI_NSS_SOFT;
	hspi2.Init.BaudRatePrescaler = SPI_BAUDRATEPRESCALER_2;
	hspi2.Init.FirstBit = SPI_FIRSTBIT_MSB;
	hspi2.Init.TIMode = SPI_TIMODE_DISABLE;
	hspi2.Init.CRCCalculation = SPI_CRCCALCULATION_DISABLE;
	hspi2.Init.CRCPolynomial = 15;
	if (HAL_SPI_Init(&hspi2) != HAL_OK)
	{
		Error_Handler();
	}

}

/* TIM1 init function */
static void MX_TIM1_Init(void)
{

	TIM_MasterConfigTypeDef sMasterConfig;
	TIM_IC_InitTypeDef sConfigIC;

	htim1.Instance = TIM1;
	htim1.Init.Prescaler = 0;
	htim1.Init.CounterMode = TIM_COUNTERMODE_UP;
	htim1.Init.Period = 0;
	htim1.Init.ClockDivision = TIM_CLOCKDIVISION_DIV1;
	htim1.Init.RepetitionCounter = 0;
	if (HAL_TIM_IC_Init(&htim1) != HAL_OK)
	{
		Error_Handler();
	}

	sMasterConfig.MasterOutputTrigger = TIM_TRGO_RESET;
	sMasterConfig.MasterSlaveMode = TIM_MASTERSLAVEMODE_DISABLE;
	if (HAL_TIMEx_MasterConfigSynchronization(&htim1, &sMasterConfig) != HAL_OK)
	{
		Error_Handler();
	}

	sConfigIC.ICPolarity = TIM_INPUTCHANNELPOLARITY_RISING;
	sConfigIC.ICSelection = TIM_ICSELECTION_DIRECTTI;
	sConfigIC.ICPrescaler = TIM_ICPSC_DIV1;
	sConfigIC.ICFilter = 0;
	if (HAL_TIM_IC_ConfigChannel(&htim1, &sConfigIC, TIM_CHANNEL_1) != HAL_OK)
	{
		Error_Handler();
	}

	if (HAL_TIM_IC_ConfigChannel(&htim1, &sConfigIC, TIM_CHANNEL_2) != HAL_OK)
	{
		Error_Handler();
	}

	if (HAL_TIM_IC_ConfigChannel(&htim1, &sConfigIC, TIM_CHANNEL_3) != HAL_OK)
	{
		Error_Handler();
	}

	if (HAL_TIM_IC_ConfigChannel(&htim1, &sConfigIC, TIM_CHANNEL_4) != HAL_OK)
	{
		Error_Handler();
	}

}

/* TIM5 init function */
static void MX_TIM5_Init(void)
{

	TIM_MasterConfigTypeDef sMasterConfig;
	TIM_OC_InitTypeDef sConfigOC;

	htim5.Instance = TIM5;
	htim5.Init.Prescaler = 0;
	htim5.Init.CounterMode = TIM_COUNTERMODE_UP;
	htim5.Init.Period = 125000;
	htim5.Init.ClockDivision = TIM_CLOCKDIVISION_DIV1;
	if (HAL_TIM_PWM_Init(&htim5) != HAL_OK)
	{
		Error_Handler();
	}

	sMasterConfig.MasterOutputTrigger = TIM_TRGO_RESET;
	sMasterConfig.MasterSlaveMode = TIM_MASTERSLAVEMODE_DISABLE;
	if (HAL_TIMEx_MasterConfigSynchronization(&htim5, &sMasterConfig) != HAL_OK)
	{
		Error_Handler();
	}

	sConfigOC.OCMode = TIM_OCMODE_PWM1;
	sConfigOC.Pulse = 0;
	sConfigOC.OCPolarity = TIM_OCPOLARITY_HIGH;
	sConfigOC.OCFastMode = TIM_OCFAST_DISABLE;
	if (HAL_TIM_PWM_ConfigChannel(&htim5, &sConfigOC, TIM_CHANNEL_1) != HAL_OK)
	{
		Error_Handler();
	}

	if (HAL_TIM_PWM_ConfigChannel(&htim5, &sConfigOC, TIM_CHANNEL_2) != HAL_OK)
	{
		Error_Handler();
	}

	if (HAL_TIM_PWM_ConfigChannel(&htim5, &sConfigOC, TIM_CHANNEL_3) != HAL_OK)
	{
		Error_Handler();
	}

	if (HAL_TIM_PWM_ConfigChannel(&htim5, &sConfigOC, TIM_CHANNEL_4) != HAL_OK)
	{
		Error_Handler();
	}

	HAL_TIM_MspPostInit(&htim5);

}
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

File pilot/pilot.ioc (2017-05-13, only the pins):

Mcu.UserName=STM32F410RBTx
PA0-WKUP.Signal=S_TIM5_CH1
PA1.Signal=S_TIM5_CH2
PA10.Signal=S_TIM1_CH3
PA11.Signal=S_TIM1_CH4
PA13.Signal=SYS_JTMS-SWDIO
PA14.Signal=SYS_JTCK-SWCLK
PA15.Signal=SYS_JTDI
PA2.Signal=S_TIM5_CH3
PA3.Signal=S_TIM5_CH4
PA4.Signal=GPIO_Output
PA5.Signal=SPI1_SCK
PA6.Signal=SPI1_MISO
PA7.Signal=SPI1_MOSI
PA8.Signal=S_TIM1_CH1
PA9.Signal=S_TIM1_CH2
PB10.Signal=I2C2_SCL
PB11.Signal=I2C2_SDA
PB12.Signal=GPIO_Output
PB13.Signal=SPI2_SCK
PB14.Signal=SPI2_MISO
PB15.Signal=SPI2_MOSI
PB3.Signal=SYS_JTDO-SWO
PB4.Signal=SYS_JTRST
PB6.Signal=USART1_TX
PB7.Signal=USART1_RX
PB8.Signal=I2C1_SCL
PB9.Signal=I2C1_SDA
PC0.Signal=ADCx_IN10
PC4.Signal=GPXTI4
PC5.Signal=GPIO_Output
PC6.Signal=USART6_TX
PC7.Signal=USART6_RX

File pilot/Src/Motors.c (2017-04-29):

#include "Motors.h"

static TIM_HandleTypeDef* _htim;

#define PERIOD_MIN			50000
#define PERIOD_MAX			100000
#define PERIOD_RESOLUTION	(PERIOD_MAX - PERIOD_MIN)
#define MAX_VALUE			1000

// TODO currently using the PWM mode there's a delay from calling start to when the actual signal starts, depends on  ARR - CCRx

void Motors_Init(TIM_HandleTypeDef* htim)
{
	_htim = htim;
	
	_htim->Instance->CCR1 = PERIOD_MIN;
	_htim->Instance->CCR2 = PERIOD_MIN;
	_htim->Instance->CCR3 = PERIOD_MIN;
	_htim->Instance->CCR4 = PERIOD_MIN;
	
	HAL_TIM_PWM_Start(_htim, TIM_CHANNEL_1);
	HAL_TIM_PWM_Start(_htim, TIM_CHANNEL_2);
	HAL_TIM_PWM_Start(_htim, TIM_CHANNEL_3);
	HAL_TIM_PWM_Start(_htim, TIM_CHANNEL_4);
}

void Motors_Set(float* values)
{
	for (int i = 0; i < 4; i++)
	{
		float value = values[i];
		
		if (value > MAX_VALUE)
			value = MAX_VALUE;
		
		int output = PERIOD_MIN + ((PERIOD_RESOLUTION / MAX_VALUE) * value);
		
		switch (i)
		{
		case 0:
			_htim->Instance->CCR1 = output;
			break;
		case 1:
			_htim->Instance->CCR2 = output;
			break;
		case 2:
			_htim->Instance->CCR3 = output;
			break;
		case 3:
			_htim->Instance->CCR4 = output;
			break;
		}
	}
}

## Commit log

2017-04-17 configure timers
2017-04-17 completed motors
2017-04-17 connected PID loop
2017-04-17 reading SBUS with DMA
2017-04-18 uart signal inverter; battery measurement
    [Board.sch]
2017-04-18 inverter gate is now optional
    [Board.sch]
2017-04-18 pcb rev2, work in progress
    [Board.kicad_pcb, Board.sch]
2017-04-19 removed GPIO headers
    [Board.sch]
2017-04-19 added MS5611 component
    [Board.sch]
2017-04-19 added mag 3110 component
    [Board.sch]
2017-04-20 replaced barometer
    [Board.sch]
2017-04-20 decouple cap
    [Board.sch]
2017-04-20 smaller JTAG pin
    [Board.sch]
2017-04-20 removed NRST global labl
    [Board.sch]
2017-04-20 new pcb
    [Board.kicad_pcb, Board.sch]
2017-04-21 assigned the new footprint
    [Board.kicad_pcb, Board.sch]
2017-04-21 organized the board a bit
    [Board.kicad_pcb, Board.sch]
2017-04-23 a bit more order
    [Board.kicad_pcb]
2017-04-23 using resistor array for I2C pullups
    [Board.kicad_pcb, Board.sch]
2017-04-23 put everything togheter
    [Board.kicad_pcb]
2017-04-24 rounded corners
    [Board.kicad_pcb]
2017-04-24 mounting holes
    [Board.kicad_pcb]
2017-04-24 a bit of reorganization
    [Board.kicad_pcb]
2017-04-24 started routing
    [Board.kicad_pcb]
2017-04-24 more routes
    [Board.kicad_pcb]
2017-04-24 outing mag
    [Board.kicad_pcb]
2017-04-24 finished routing
    [Board.kicad_pcb]
2017-04-24 moved some floating vias
    [Board.kicad_pcb]
2017-04-24 via stiching?
    [Board.kicad_pcb]
2017-04-24 added via stiching
    [Board.kicad_pcb]
2017-04-24 exposed another UART
    [Board.kicad_pcb, Board.sch]
2017-04-24 silk screen items
    [Board.kicad_pcb]
2017-04-25 input/output silkscreen
    [Board.kicad_pcb]
2017-04-25 fixed a few unconnected pads
    [Board.kicad_pcb]
2017-04-25 more silkscreen
    [Board.kicad_pcb]
2017-04-25 moved a bit more silkscreen
    [Board.kicad_pcb]
2017-04-29 back to using PWM because OneShot125 had some problem with implementation
    [Motors.c, main.c, pilot.ioc]
2017-04-29 calculating accel and gyro bias
2017-04-30 applying accel and gyro biases locally
2017-05-01 using different UART for debugging
2017-05-01 moved calibrate to a different function
2017-05-01 back to using regular mode instead of DMA for UART6
2017-05-01 seperated calibrate and eeprom
2017-05-09 reading baro data with I2C
2017-05-09 magnetometer I2C test
2017-05-09 I2C fast mode
2017-05-13 added battery voltage monitoring via ADC
2017-05-13 now printing up tp 2 decimal places to minimize UART traffic
2017-05-13 forgot to add this to the ADC commit
2017-05-13 adjusted motor mixxing
2017-05-13 inverter was connected wrong
    [Board.sch]
2017-05-13 fixed inverter connections
    [Board.kicad_pcb]
2017-05-13 fixed some stupid mistakes, NOW IT FINALLY WORKS
    [main.c]

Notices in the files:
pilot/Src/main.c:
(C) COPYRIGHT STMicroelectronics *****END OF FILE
